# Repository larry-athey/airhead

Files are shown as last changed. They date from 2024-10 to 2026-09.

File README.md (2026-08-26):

# Airhead
Air Still (or clone) upgrade that uses a low-speed PWM driven SSR for heating element control and an ESP32 to make the whole thing smarter. Eliminates that constant full power on/off switching to the heating element and the possibility of scorching. Plus even more features.

You may contact me directly at https://panhandleponics.com<br>
Subscribe to the official YouTube channel at https://www.youtube.com/@PanhandlePonics<br>

_**NEWSFLASH:** If you'd like a far more advanced stand-alone WiFi enabled version of the temperature/power controller that I designed here with the addition of PID for brewing/mashing, check out my [Boilermaker](https://github.com/larry-athey/boilermaker) project!_

**Facebook Idiot:** _Why would you bother?_<br>
**Me:** It's only a "bother" for somebody who couldn't do it on their best day. I'd rather have nicer things.

_...No, I don't use AI to design and build my projects, I actually still know how to use my brain..._

---

Still Spirits brand Air Stills and the various clones all suffer the same design flaw where the temperature is managed the same way it is with an electric cooking appliance. This also includes the ones with adjustable temperature. They send full power to the heating element when heating up, shut it off when they're up to temperature, then repeat this cycle. Thanks for the unstable yo-yo temperatures!

If you have any suspended solids in your wash, they will scorch and fuse to the bottom as they fall out of solution. This will add foul flavors to anything that you're distilling, especially gin. As with my [RPi-Smart-Still](https://github.com/larry-athey/rpi-smart-still) project, this problem is solved by replacing the relays or snap switches on the heating element with a custom low speed PWM _(0.20 Hz)_ and a solid state relay that pulses the power.

As long as the heating element is always running even just a little bit, it will radiate heat upward and force most of the suspended solids to stay afloat. This will eliminate the possibility of scorching for the most part. Just don't try to fill your still with a thick goopy mash.

This project aims to solve that problem and add three user selectable modes:

1. Operate at a constant user selectable power level (1% to 100%)
2. Operate at a constant user selectable temperature (up to 100C/212F)
3. Perform timed runs with a user selectable starting and ending temperature

_Refer to the [Airhead Operation](https://github.com/larry-athey/airhead/blob/main/Instructions/Operation.md) guide for more information on these three modes._

The greatest benefit of the custom low speed PWM and SSR is that it doesn't contribute to premature heating element failure as with the high-speed on/off switching in SCR controllers. SCR phase-angle control generates harmonics _(distortions in the AC sine wave)_ which leads to uneven current distribution, physical vibration, and stress within a heating element. The Airhead is actually better for your boiler's longevity!

The technical definition of the temperature controller in the Airhead is a PI controller, there is no D _(derivative gain)_. The reason for this is because PID controllers will spend more time off than on, once the boiler is up to temperature. This is bad for distillation because there's no thermal velocity to push the ethanol upward out of your wash. The Airhead is intentionally thermally aggressive, unlike a PID controller.

The brains of the operation is a [LilyGo T-Display-S3](https://www.amazon.com/gp/product/B0BLNKPL25/) ESP32 microcontroller with a built-in capacitive touch color LCD display. The boiler control code is a port of the code from my [RPi-Smart-Still](https://github.com/larry-athey/rpi-smart-still) project. This means that even though this is a newer project, the code has already been refined and fine tuned for 2 years in advance.

Refer to the contents of the **/Diagrams/** and **/Instructions/** directories here to learn how to build this project, and be sure to check out the [FAQ](https://github.com/larry-athey/airhead/blob/main/Instructions/FAQ.md).

_**NOTE:** Turn-key kits for those not comfortable with building this from scratch are now available from [my website](https://panhandleponics.com/technology-assisted-distillation/). There may be a short lead time on orders to allow for 3D printing of the 3D models or parts restocking. You may also drop-ship your air still clone to me to have the Airhead upgrade installed and tested with an actual run before I send it to you ready to roll! And it still works out to be less expensive than an original Air Still!_<br><br>

<br><br>
<br><br>
<br><br>
<br><br>
<br>

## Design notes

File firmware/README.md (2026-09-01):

# Firmware Updating

As of the Airhead v1.0.2a source code, end users can now update their firmware over-the-air using a web browser. The initial plan was to provide a USB firmware update utility, but the one that Espressif provides doesn't work like the Arduino IDE does and requires the user to perform circus tricks and learn to use a cryptic program that no non-techie will ever bother with.

To put the Airhead into firmware update mode, turn on the power then press and hold the **Value-** button as soon as the screen lights up. When you see the banner on the screen that says **"Firmare Update Mode"** you can let go of the button.

The Airhead will start up a WiFi access point with the SSID **"Airhead-Firmware-Updater"** and the password to connect is **"12345678"**. Keep in mind that the Airhead is working without an external antenna, so the reliable WiFi range is limited to just a few feet.

Start your web browser and go to **http://192.168.4.1**

<br>

If you are unable to connect, check to make sure that your device pulled an IP address from the Airhead. If it does not pull one, you will need to manually configure a static IP address on your device. Here are settings that will work for you if you encounter this problem.

Address: 192.168.4.100<br>
Subnet Mask: 255.255.255.0<br>
Gateway: 192.168.4.1<br>
DNS: 192.168.4.1<br>

Click on the button to browse to your **airhead-firmware.bin** file and click the blue button to start the upload.

Once the upload progress bar has completed, the Airhead will reboot and will be running the new firmware.

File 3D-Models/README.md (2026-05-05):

All Airhead related 3D models were created by [James "The Doc"](https://www.youtube.com/@TheDocChannel) from Ireland. Keep in mind that the 3D models for the spacer ring halves may require rotation in Cura _(or whatever slicer you use)_ in order to fit on your print bed. The full spacer ring will require a printer with at least a 300x300 mm bed.

The model **Airhead Inside Plate.stl** is only necessary if you are installing an Airhead in a metal Air Still clone that came with a built-in adjustable temperature controller. Removing the stock controller leaves a large rectangular hole where the bolt holes would be drilled in a plastic-body clone. This plate covers that hole from the inside and provides the two bolt holes and a wire pass-thru hole.

3D models in the **uBM** folder are for the μBoilermaker (Micro Boilermaker), see [uBoilermaker.md](https://github.com/larry-athey/airhead/blob/main/Instructions/uBoilermaker.md) for more information.

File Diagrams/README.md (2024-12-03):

The schematic for the PSU and interface is just for the most basic connection using a solid state relay. If you intend to use an SCR board, there may or may not be additional components involved.

If you are using a PWM controlled SCR board, chances are that it already has an opto isolator onboard to protect the original PWM controller that it was designed for. No additional circuity should be needed.

If you are using a voltage controlled SCR board, you will need an optically isolated [PWM to voltage convertor](https://www.amazon.com/dp/B0BG2G5FMX) which will require an additional buck regulator due to its power supply requirements.

_**NOTE:** If you are going to be using an SCR board of any type, you will need uncomment the **SCR_OUT** constant in the ESP32 code in order to enable the 2 KHz PWM output. The default 0.20 Hz PWM used for SSR support is far too slow for use with any SCR board._

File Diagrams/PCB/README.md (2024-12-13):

Printed circuit board for the Airhead PSU and Interface, designed by [James "The Doc"](https://www.youtube.com/@TheDocChannel) from Ireland. This PCB supports PWM or voltage controlled SCR boards, and can be used with a solid state relay by simply soldering wires to the board to connect to the control side of your SSR. These wires would be connected to any ground hole and the center pin for the PWM/+5V jumper.

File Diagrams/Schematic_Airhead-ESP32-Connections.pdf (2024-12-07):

A | A

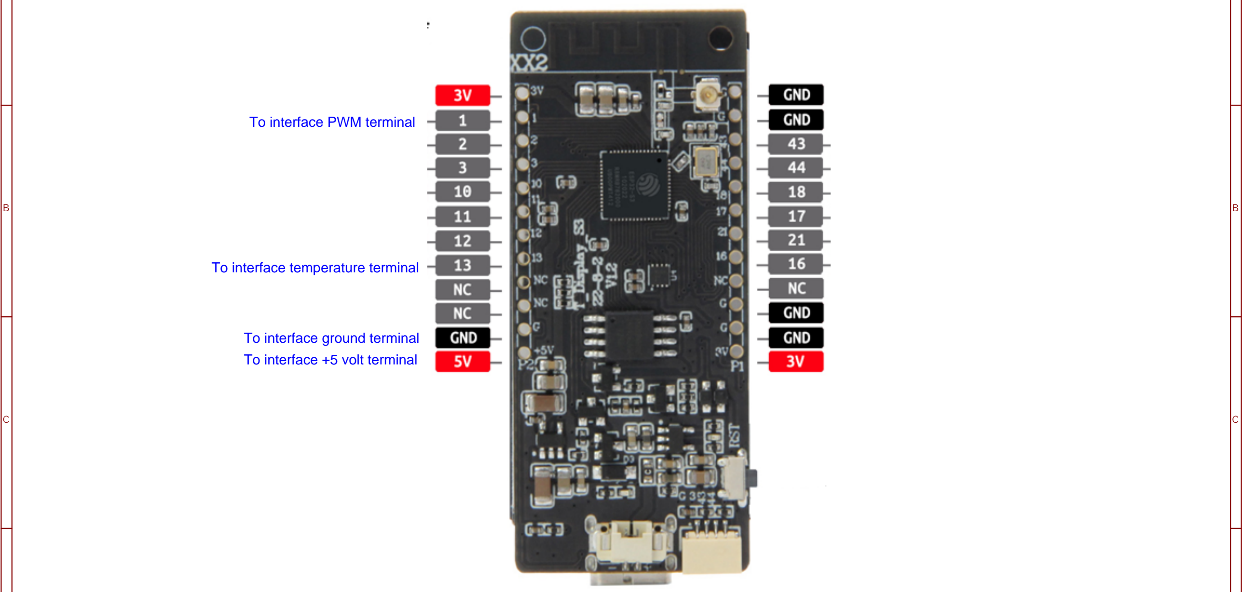
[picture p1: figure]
To interface +5 volt terminal; To interface ground terminal; To interface temperature terminal; To interface PWM terminal

D | D

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
TITLE:
Airhead ESP32 Connections | REV: 1.0
Date: | 2024-12-02

Sheet: 1/1
Drawn By: Larry Athey

Company: Panhandle Ponics R&D

LilyGo T-Display-S3 Bottom View

USB-C Port

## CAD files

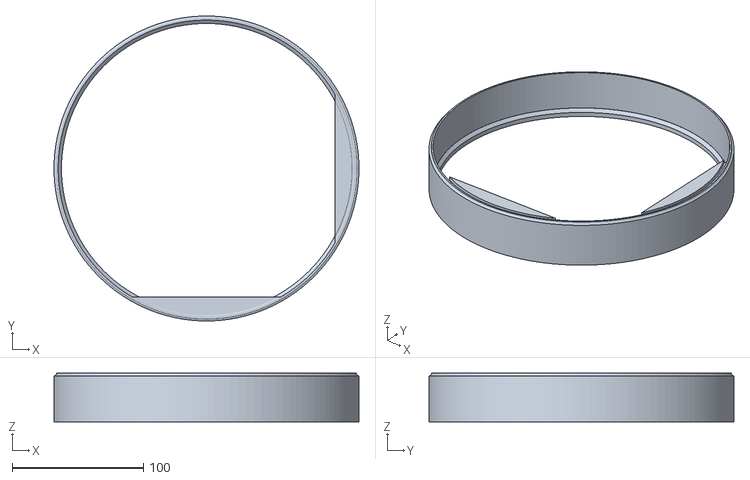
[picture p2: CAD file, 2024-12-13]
3D-Models/Air Still Spacer Ring/Spacer Ring Full.stl
232.3 x 232.3 x 37.0

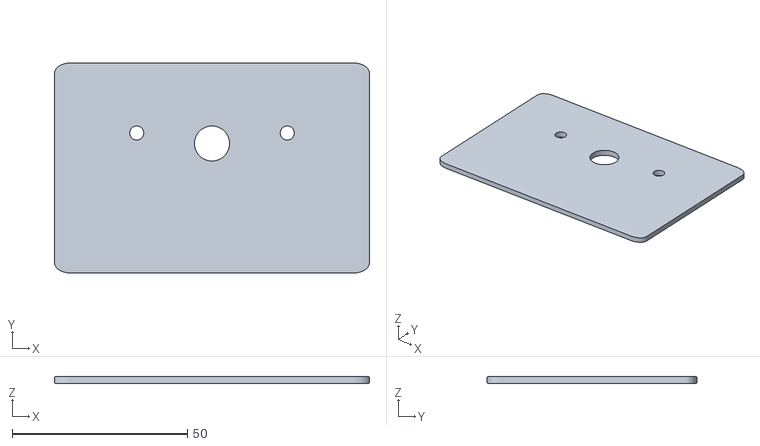
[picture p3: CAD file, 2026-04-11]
3D-Models/Airhead Inside Plate.stl
90.0 x 60.0 x 2.00

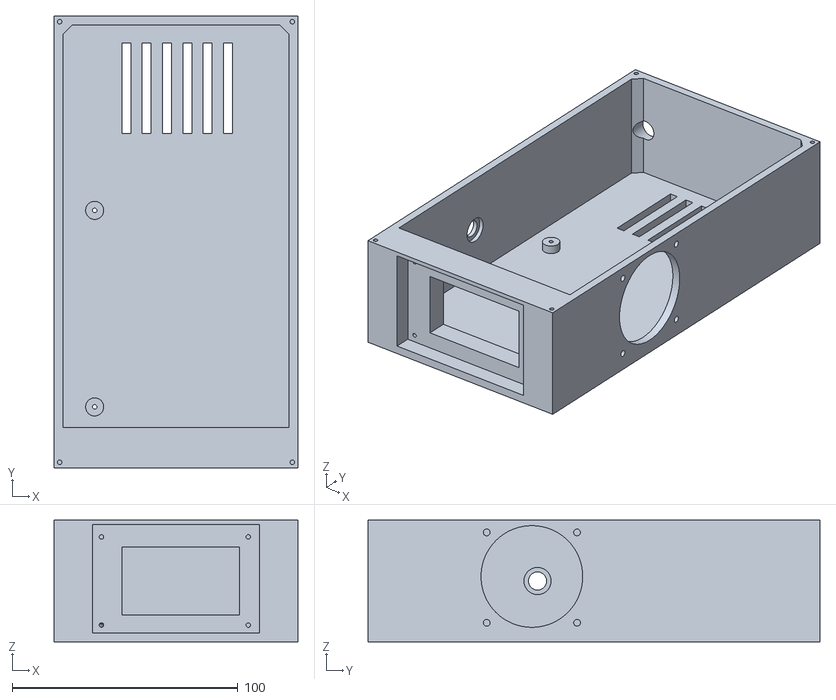
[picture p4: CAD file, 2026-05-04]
3D-Models/uBM/uBM-Case-Bottom.stl
108.0 x 200.0 x 54.0

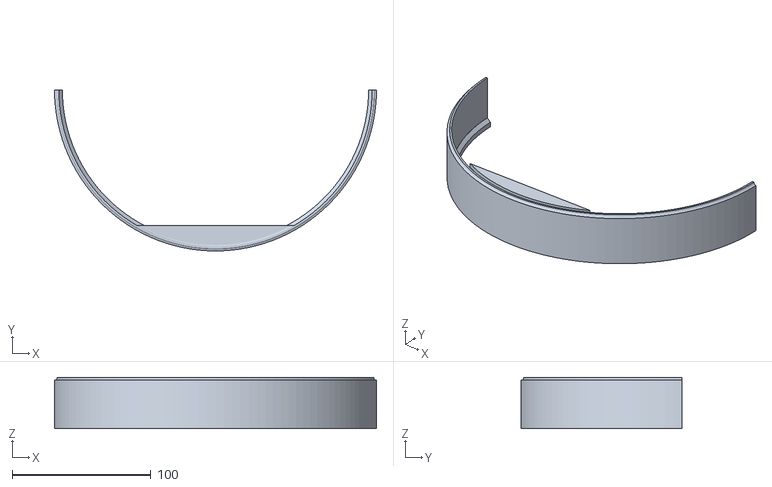
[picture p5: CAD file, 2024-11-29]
3D-Models/Air Still Spacer Ring/Spacer Ring Half.stl
232.3 x 116.1 x 37.0

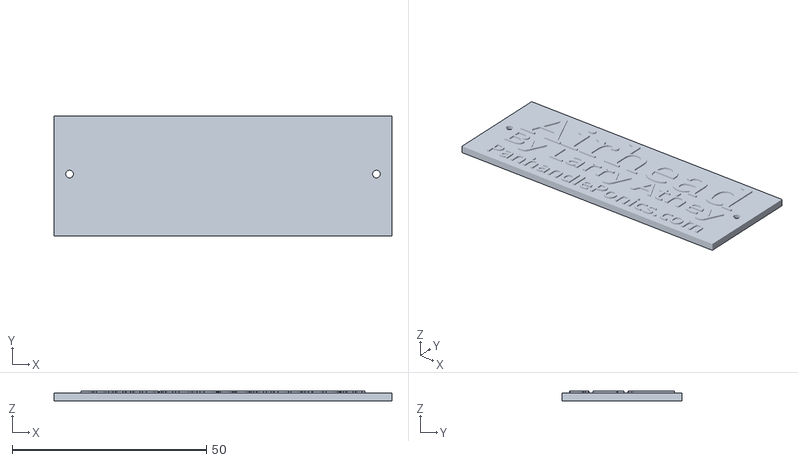
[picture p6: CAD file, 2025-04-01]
3D-Models/Airhead-Badge.stl
87.0 x 31.0 x 2.50

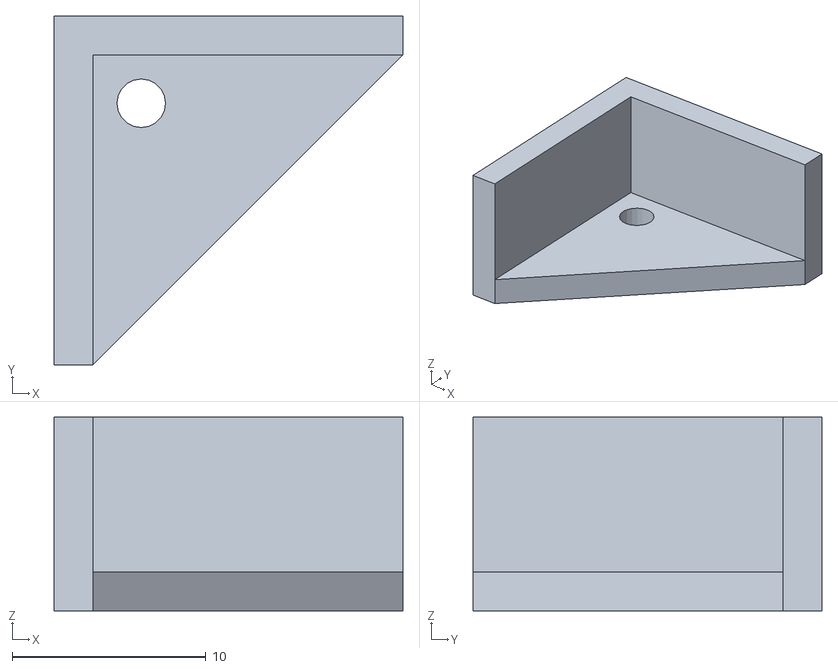
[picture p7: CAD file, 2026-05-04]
3D-Models/uBM/uBM-Corner-Cap.stl
18.0 x 18.0 x 10.0

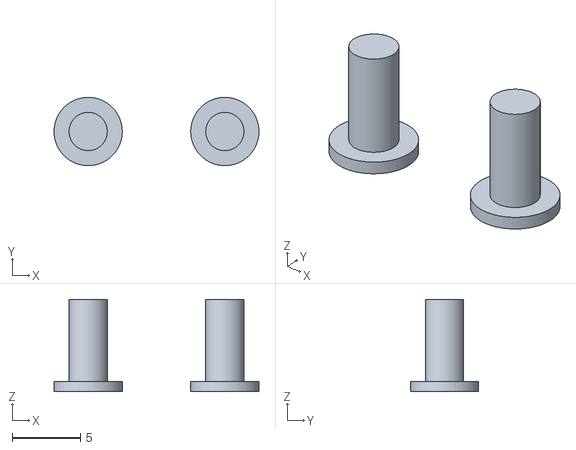
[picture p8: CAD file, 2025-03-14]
3D-Models/Airhead-Buttons.stl
15.0 x 5.00 x 6.75

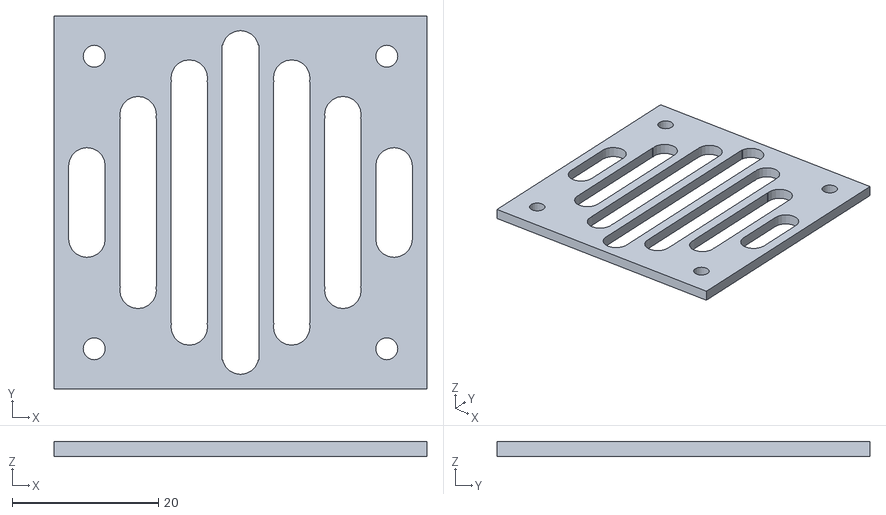
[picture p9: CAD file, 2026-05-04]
3D-Models/uBM/uBM-Fan-Cover.stl
51.0 x 51.0 x 2.00

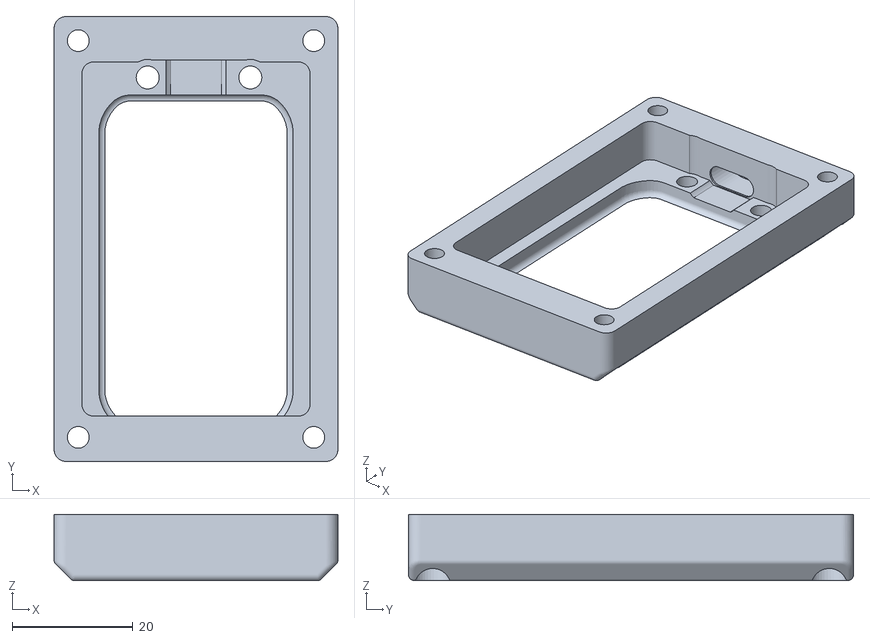
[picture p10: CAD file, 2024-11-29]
3D-Models/Airhead Case Front.stl
47.0 x 73.7 x 11.0

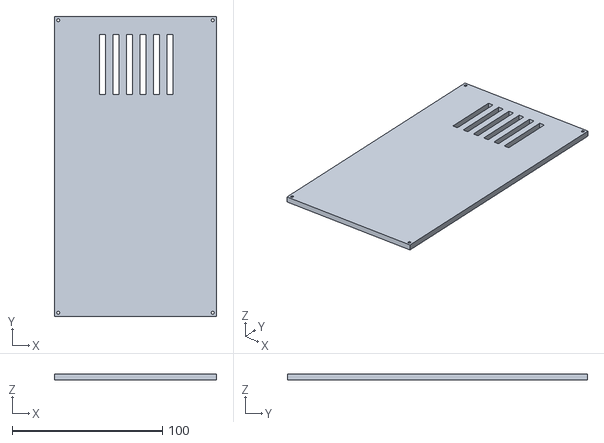
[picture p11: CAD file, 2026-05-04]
3D-Models/uBM/uBM-Case-Top.stl
108.0 x 200.0 x 4.00

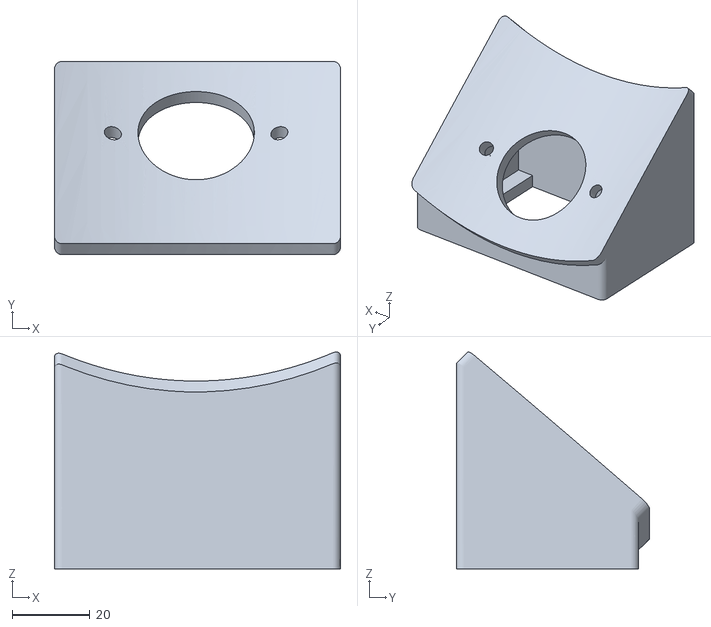
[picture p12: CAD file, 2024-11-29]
3D-Models/Airhead Case Back.stl
73.7 x 49.8 x 55.9

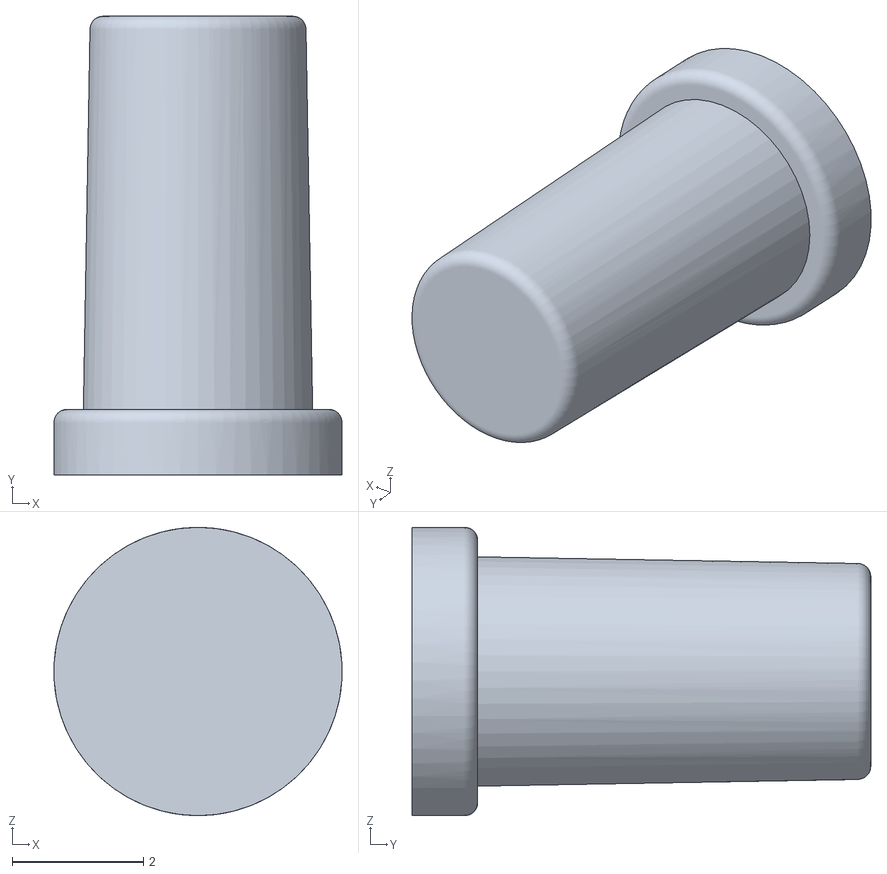
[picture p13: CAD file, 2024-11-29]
3D-Models/Airhead Button.stl
4.40 x 7.00 x 4.40

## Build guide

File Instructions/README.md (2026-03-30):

# Airhead Turn-Key Kit

For those who aren't up to [component level](https://github.com/larry-athey/airhead/tree/main/Instructions/DIY-Build) electronics work and 3D printing, [Airhead turn-key kits](https://panhandleponics.com/technology-assisted-distillation/) are available from my website for $140 plus shipping in the USA where the USPS flat-rate box coverage area applies. Installation requires no soldering and only basic tools. Orders to Alaska and Hawaii require a special URL to be emailed to you due to the added shipping expense.

Please keep in mind that I'm not running a full blown mail-order operation. I only have four 3D printers and only one that is large enough to print the Airhead spacer ring. Each of these kits take 12 hours to print all parts, so I'm only capable of building and testing one Airhead every 3 days. My other three printers are pretty much dedicated to printing [Boilermaker](https://github.com/larry-athey/boilermaker) cases which I can also only build and test one every 3 days.

# Installation Guide Video

I have put together the video [Airhead Installation Using a Vevor Air Still](https://youtu.be/vFivj2nX99s) to show people how to install the Airhead Turn-Key Kit in a Vevor water distiller. I also offer people the option to drop-ship their Vevor air still clones to me to have the Airhead installed and tested with an actual run before shipping it out to them. It's only slightly more than the price of the kit alone and saves you the trouble of installing it yourself. Again, orders to Alaska and Hawaii require additional shipping fees.

I also put together the video [Airhead + Air Still Full Demo](https://www.youtube.com/watch?v=bEKPDaXU4ro) that shows how to use the Airhead after it's installed. This example shows how to distill wine in order to get high-proof brandy out of it. You can also use the Airhead to make gin and to even clean up whiskey that you may have over-oaked. Just make sure that the overall body of liquid in the still is no more than 40% ABV or things could go BOOM!

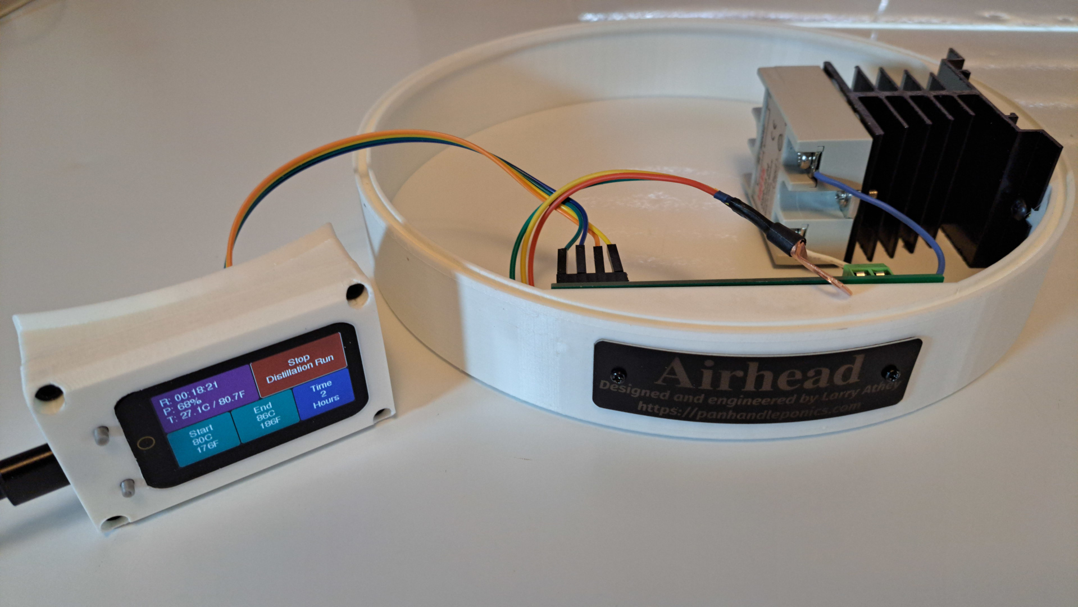
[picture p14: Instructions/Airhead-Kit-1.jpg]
<br>

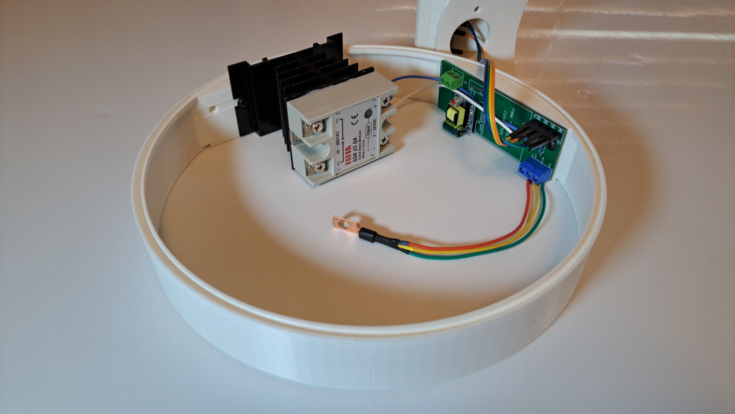
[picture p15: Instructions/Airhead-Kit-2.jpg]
<br>

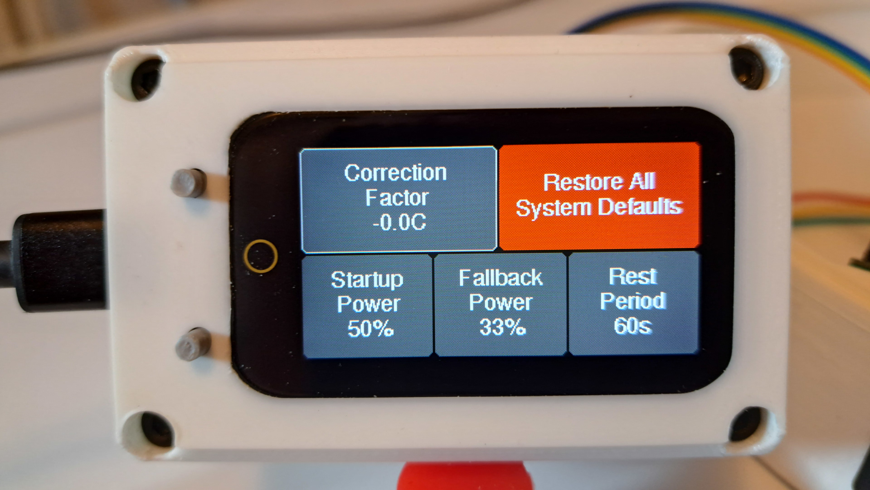
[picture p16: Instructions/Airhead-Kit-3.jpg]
<br>

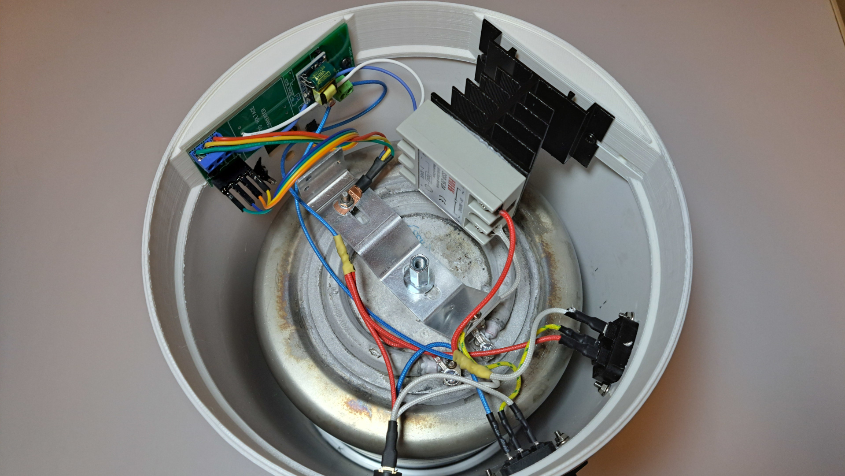
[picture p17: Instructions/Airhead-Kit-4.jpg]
<br>

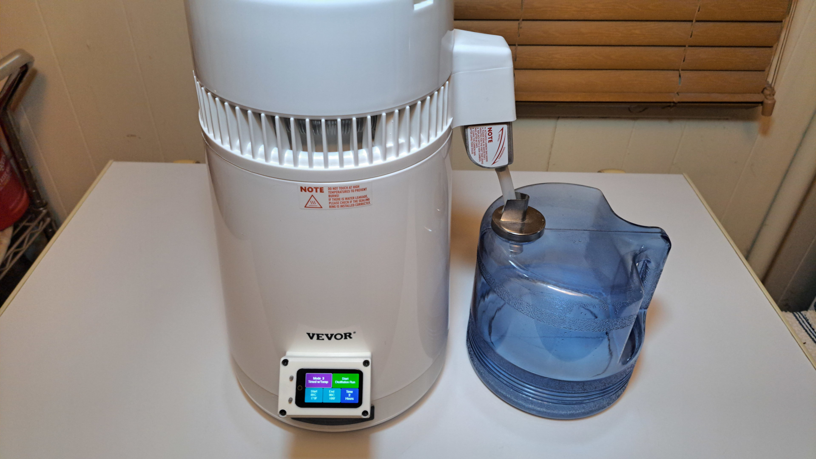
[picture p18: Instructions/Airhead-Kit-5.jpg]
<br>

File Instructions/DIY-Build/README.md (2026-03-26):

# DIY Build Assembly Instructions

_The following instructions are for **modifying** an Air Still (or clone). Personally, I would recommend just gutting the unit and rewiring the unit from scratch according to the [Airhead Implementation](https://github.com/larry-athey/airhead/blob/main/Diagrams/Schematic_Airhead-Implementation.pdf) schematic without the temperature snap switch or the circuit breaker that kicks if it boils dry. The Airhead Code already has protection built-in that shuts down the run if the boiler temperature exceeds 103C/217F. It's clear that these devices are not built to any solid standards, so it's really not possible to create a one-size-fits-all set of modification instructions._

In these examples, I'm using a cheap $65 [Vevor water distiller](https://www.amazon.com/dp/B0CN2SBJLT). No need for an expensive original Air Still for this project. For the sake of simplicity, I will be setting up this Air Still clone to use a solid state relay as a simlified PID controller rather than an SCR board. You can also use a solid state relay like an SCR board at a much lower frequency, refer to the source code comments. Anyway, the first step is to turn your Air Still upside down and remove the bottom cover.

Referring to the photo **Air-Still-Default-Wiring.jpg** here. The white wires are connected to the thermal control snap switch and are the AC neutral connection to the heating element. The blue wires are for an LED power indicator on the front of the still. The red wires are from the AC hot side and go to a circuit breaker on the front of the still and then come back to connect to the other side of the heating element. Lastly, the yellow wires are the earth ground of the AC connection and connect to the body of the boiler vessel.

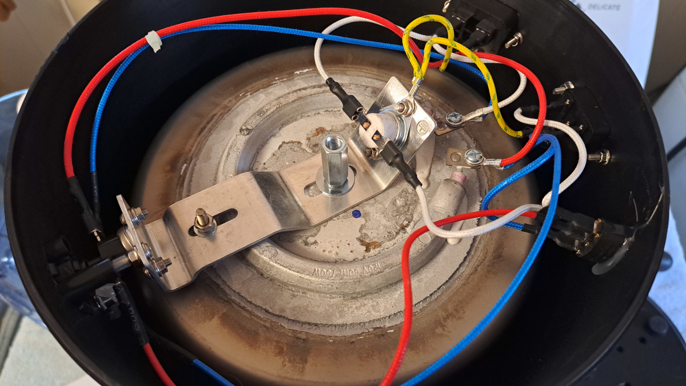
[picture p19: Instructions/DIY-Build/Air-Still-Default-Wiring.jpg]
<br>

You will now need to remove that aluminum bracket so you can remove the power indicator, the button for the reset breaker, and the snap switch that currently controls the temperature. We will not be removing the reset breaker, but it will likely never be used since the Airhead brain will shut down the unit if it ever goes over 103C/217F. You can clip the wires to the power indicator and strip them back since they will be used to power the Airhead controller system. The wires to the snap switch will be connected to the solid state relay.

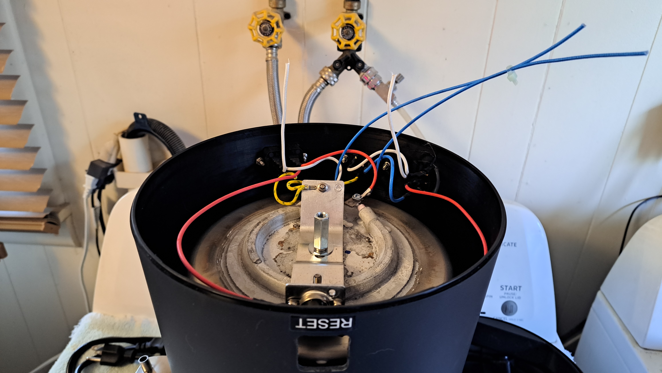
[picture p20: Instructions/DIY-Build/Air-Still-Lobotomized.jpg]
<br>

As you can see in the photo **Air-Still-Lobotomized.jpg** above, everything that I mentioned has been removed and the aluminum bracket has been put back in place. I slid it back as far as it would go since the reset breaker will likely never need to be used unless something goes seriously wrong. We have the blue wires that will be connected to the Airhead power supply and interface board, and the white wires which will be connected to the load side of the solid state relay. You may or may not need to extend the white wires.

_**NOTE:** Depending on your Air Still (or clone) model, the manufacturer may have put the fan on the switched side of the heating element. This is an absolutely stupid plan, the fan should run continuously. The temperature control should only run the heating element. This will require a simple wiring modification if yours has this problem. Lucky me, this unit actually has that exact design flaw._

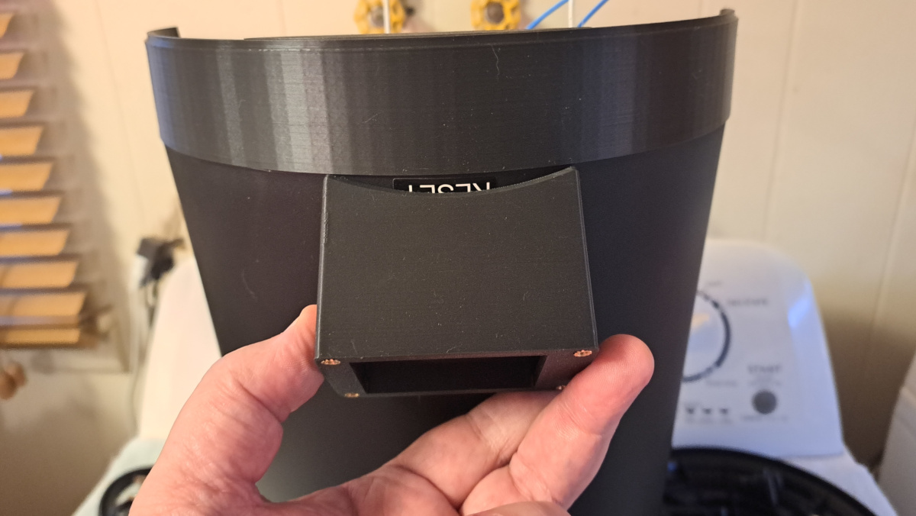
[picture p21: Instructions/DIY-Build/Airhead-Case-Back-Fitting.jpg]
<br>

As demonstrated in the photo **Airhead-Case-Back-Fitting.jpg** above, you need to align the back part of your Airhead case over the hole that the reset button was removed from. It's best if you set your spacer ring in place to get your vertical alignment correct. You should mark the two screw holes using a pencil, or small paint brush and paint, or nail polish if you happen to have that at home. Carefully drill the holes while avoiding damage to the boiler vessel inside. Then attach the case with nuts and bolts, paint the threads to lock the nuts in place.

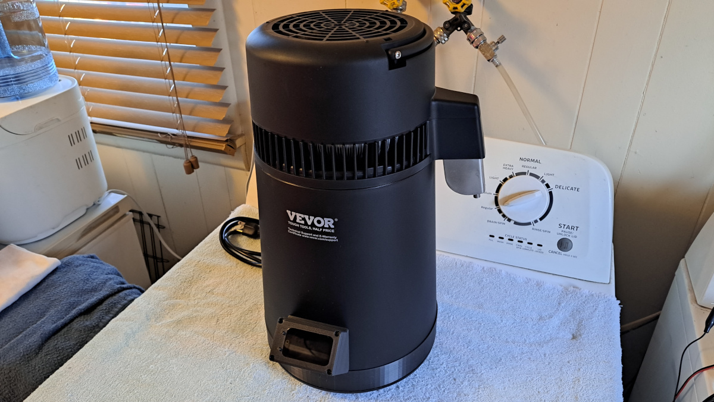
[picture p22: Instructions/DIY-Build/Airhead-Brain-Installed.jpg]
<br>

As you can see in the photo **Airhead-Brain-Installed.jpg** above, the Airhead brain is installed in its case and it doesn't interfere with the seating of the spacer ring. This is just a dry fitting test before we procede with the wiring. Please keep in mind that the wiring steps that follow are using a prototype power supply and interface board. The Airhead kits that I will be selling on my website will come with an actual custom designed printed circuit board. I just don't have them at this time since they have to be ordered from China in bulk.

_**NOTE:** If you are using the same Air Still clone that I'm using, you will need a [6mm-1.00x70mm bolt](https://www.amazon.com/VGBUY-Stainless-Spanner-Included-VG30115/dp/B0CK1RQWGH/) to reattach the bottom after the spacer ring is in place. Other brands may use a different method to attach the bottom, I have another brand that uses 3 screws._

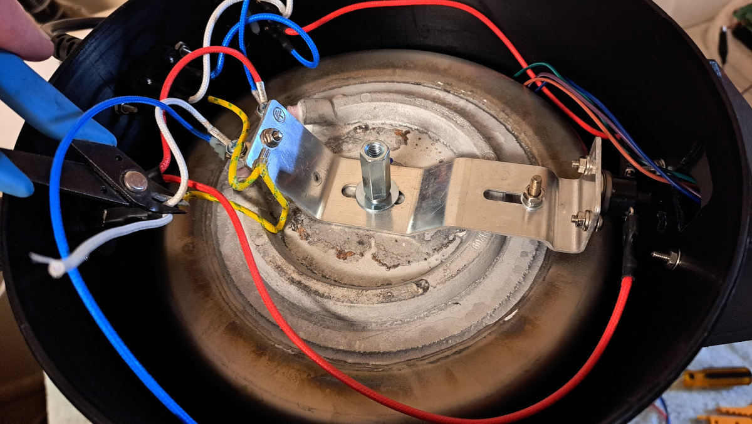
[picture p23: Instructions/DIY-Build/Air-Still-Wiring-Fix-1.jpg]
<br>

As you can see in the photo **Air-Still-Wiring-Fix-1.jpg** above, the bottom connection of the heating element has one of the blue wires and a white wire connected to it. If we were to leave things as is and connect the two white wires from the snap switch to the solid state relay, the entire system would never turn on. If it did, the entire system including the fan would turn off as soon as it's up to temperature. This is the stupid plan that I was referring to. Cut that white wire connected from the element to the fan power socket.

_**NOTE:** Don't panic, the goal here is just to have all of the neutral lines connected together, except for the neutral side of the heatng element._

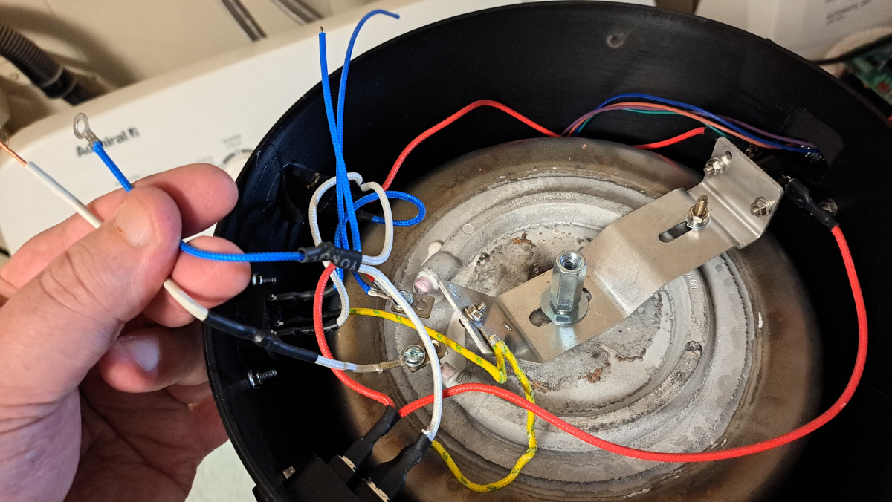
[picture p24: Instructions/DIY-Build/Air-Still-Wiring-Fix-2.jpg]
<br>

Looking at the photo **Air-Still-Wiring-Fix-2.jpg** above, you can see that the white wire that was clipped has been extended about 4 inches. This connects to one of the screws on the load side of the solid state relay. The blue wire was removed the the bottom side of the heating element, cut in half, and then joined together with the two white wires that were connected to the snap switch that was removed. The blue wire with the eyelet connector on the end connects to the other screw on the load side of the solid state relay.

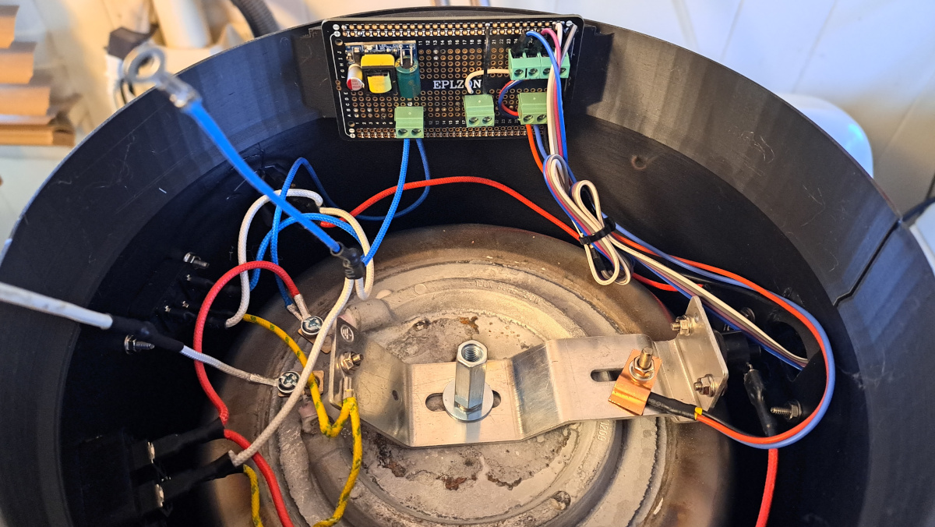
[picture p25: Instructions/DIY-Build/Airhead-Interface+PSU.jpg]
<br>

As you can see in the photo **Airhead-Interface+PSU.jpg** above, the prototype interface and PSU board has been attached to one of the spacer ring halves. The two blue wires with the stripped ends have been connected to the AC input terminals. The Airhead brain ribbon cable and the DS18B20 temperature sensor have also been connected. The temperature sensor has been installed under a copper heat sink clip against the aluminum bracket. Thermal transfer compound shouldn't be used in this case.

Airhead brain connector, left to right:
1. Temperature, ESP32 GPIO 13
2. PWM, ESP32 GPIO 1
3. +5 volts
4. Ground

Temperature sensor connector, left to right:
1. +5 volts
2. Data
3. Ground

PWM/SSR connector, left to right:
1. +3.3 volt PWM output
2. Ground

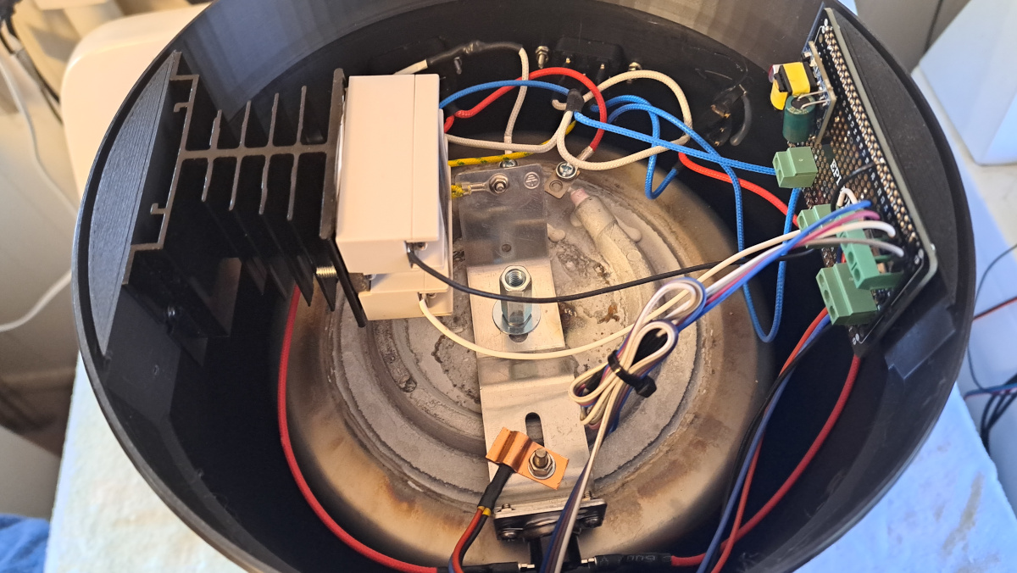
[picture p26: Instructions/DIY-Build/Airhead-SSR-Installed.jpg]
<br>

Finally, as shown in the photo **Airhead-SSR-Installed.jpg** above, the solid state relay is installed and wired in. The heat sink isn't really necessary, this SSR just came with one so I went ahead and used it to show that there actually is room for one. The documentation for these states that a heat sink isn't needed until a 1200 watt load is on it. The heating element used in these appliances is only 700 watts.

_**NOTE:** If you think your temperature sensor is picking up too much heat from the heating element in the location shown in the photos, move it over where the snap switch was installed. That region of the aluminum bracket is further away from the heating element and has more free air around the mounting point. This will tame down its readings a little bit and may be beneficial to your use of the still. If you applied thermal transfer compound, you may also want to try wiping it off test things again._

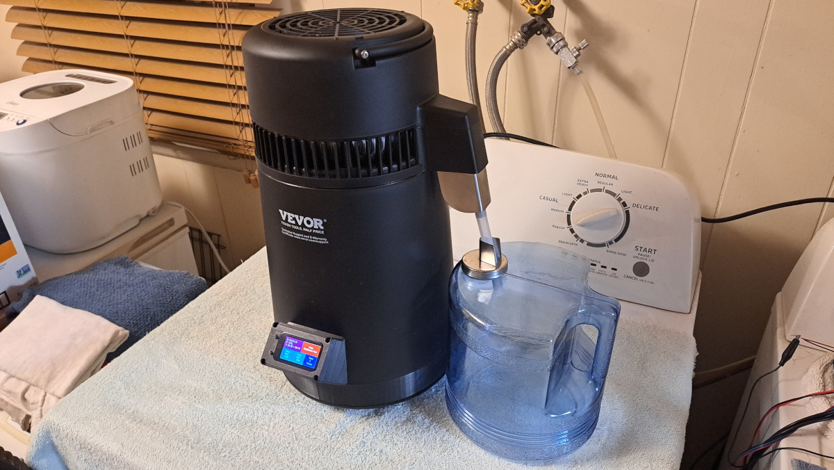
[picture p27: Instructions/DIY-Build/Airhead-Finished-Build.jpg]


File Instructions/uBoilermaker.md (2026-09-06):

# μBoilermaker (micro Boilermaker) 



---

The μBoilermaker is 100% based on the Airhead, but is a stand-alone boiler controller for 120 volt resistive loads up to 1500 watts and uses an autotuning PID controller, unlike the aggressive PI controller used by the Airhead. You can switch any Airhead to μBoilermaker mode by holding the Value+ button for 15 seconds after you have selected Mode 3. Use the same procedure to switch things back.

The reason for the μBoilermaker is to satisfy the numerous requests for a Boilermaker that isn't WiFi dependent. This isn't a one-to-one implementation of the full Boilermaker, but it provides a person the ability to have constant power, constant temperature, or timed runs with progressive temperature. It also uses a preset **Cruise Then Brew** mode and runs in PI control until 1C below the target temp.

Unlike the full Boilermaker, these are sold on my website as 120-volt-only and bench/counter top only. The size of the case only allows for 14 gauge grounded power cables and they only ship with an SSR-40DA solid state relay mounted to the same heat sink used in the Airhead. These are priced the same as the full Boilermaker with 120 volt pigtails, they're just a smaller version with a touch screen.

[Operation](https://github.com/larry-athey/airhead/blob/main/Instructions/Operation.md) of the μBoilermaker is completely identical to the Airhead, the only real difference are the options on the calibration page which are PID gain parameters. The target audience for these are people using stove-top stills with an electric hot plate, home beer brewers, and people who want far better control over an electric smoker, all without the need for a WiFi connection.

### How to run PID autotune:

1. Fill the boiler to its normal full mark with water.
2. Select Mode 3.
3. Hold **Value+** for at least 5 seconds, then press **Value-** at the same time.
4. The test takes 5–15 minutes. Watch the screen for progress.

After tuning completes, the new **P, I, and D** values will be saved. You can manually tweak them on the calibration page if needed.

### What is PID? (simple version)

PID is a control method that tries to reach and hold your exact target temperature smoothly:

- **P (Proportional)** — How strongly it reacts to being off-target.
- **I (Integral)** — Corrects small long-term errors (like slowly drifting a bit low).
- **D (Derivative)** — Looks at how fast the temperature is changing and helps prevent overshooting.

### And now the scientific version

<br>

In the Temperature Cruise mode of the full Boilermaker, the **Change Wait** and **Adjustment Rate** are equal to the **P** parameter and the **Deviation Rate** is equal to the **I** parameter. These values also exist in the Airhead's PI controller, but are static settings.

### Realistic expectations:

- PID gives very steady temperature — great for mashing, fermenting, sous-vide style control, or electric smokers.
- It is **not** as thermally aggressive as the normal Airhead PI mode. Once at temperature it will pulse the heater more gently, so you will see significantly slower vapor production in distillation.
- The temperature control becomes more stable the longer it runs because the PID is training itself on the current load.
- Autotune results are a good starting point, but every boiler/setup is different. Feel free to tweak the numbers ±20–50% and test.

_**NOTE:** If you are using an electric hot plate, you will want to bypass its internal temperature control dial or it will interrupt your power once you reach its maximum temperature. It's also recommended that you maintain good ventilation under it because most also have a thermal snap switch that will cut out if it overheats internally. The μBoilermaker does not work with inductive cooktops!_

---



---



---



---



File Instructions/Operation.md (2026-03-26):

# Airhead Operation

<br>

As you have probably noticed by the photos on the front page of this GitHub repo, the Airhead has three operating modes. Each of the modes are user configurable and your last used settings will be restored each time you start up your still. In temperature managed modes 2 and 3, the temperature is checked every 30 seconds and the power is adjusted accordingly. The temperature is managed to +/- 0.2C/0.36F in order to maintain a fair level of accuracy at temperatures down to 38C/100F without beating the CPU to death. 

**Mode 1** maintains a constant power level with no temperature management whatsoever. You may adjust the power level from 1% to 100%. This mode would be used for simmering liquids, calibrating the Correction Factor setting, or distilling water if you set the power level to 100%. There is a safety feature that will shut down your still if you boil out all of the water. This safety feature kicks in at 103C/217F.

**Mode 2** maintains a constant temperature and automatically adjusts the power. If you fill your still with room temperature wash/wine and you set the temperature to 80C/176F, it may take 30 minutes at sea level to reach the minimum operating temperature. The power level starts out at 50% and progressively increases by 1% every minute until the target temperature is reached. At that point, the power will fall back to one third (33%) and rest for 1 minute before temperature management begins. Distillate usually starts in 10 minutes.

**Mode 3** is a timed distillation run where you set a starting and ending temperature. The time is selected in hours and the target temperature is adjusted _(up or down)_ every 15 minutes. This is primarily for distilling spirits. For example, you would do a 2 hour run starting at 80C/176F and ending at 86C/186F. This is a common method used by those who bought Air Still clones with manual temperature control to squeeze out as much product as possible. This mode frees you from performing manual temperature changes.

If you are at a higher altitude, such as the "Mile High City" (Denver, CO) you will notice that water boils way faster. After your Airhead performs the 33% fallback when the minimum operating temperature is reached, you will likely see the power level adjust down instead of up. It should come as no surprise to see it adjust down to 18% to 20% to maintain water at 80C/176F, this is absolutely normal.

Keep in mind that a higher ABV wash (15% or greater) requires less heat at the beginning than a lower ABV wash. This needs to be kept in mind when you are setting your temperatures in Mode 3. If you aren't getting distillate until the end of a Mode 3 run, your ABV is too low. Increase your wash ABV or increase your temperature range.

_**NOTE:** As of the version 1.0.2 source code release, the startup and fallback power levels specified in the two temperature managed modes are now configurable. If you press the home button to the left of the screen (the gold circle) it will switch the Airhead into configuration mode. From this screen, you can configure the correction factor for the temperature sensor from -15C to +15C. You can also configure the startup and fallback power levels from 1% to 100% as well as the rest period after the boiler is up to temperature from 1 second to 255 seconds. Lastly, there is a button that also allows you to do a full reset of all settings back to their defaults._

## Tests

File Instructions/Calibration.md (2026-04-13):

# Calibration

<br>

Calibrating the correction factor of the Airhead temperature sensor is actually stupid-simple and only requires you to know your altitude above sea level. Water boils at 100C/212F at sea level and that temperature drops by 0.5C/1F for every 500 feet you are above sea level. So in my case where I'm 4000 feet above sea level, water boils at 95.5C/204F.

Keep in mind that an immersion thermometer isn't the most accurate way of comparing the readings to determine the correction factor. If you were to use one, an old analog unit that works using a bi-metal coil would be the most reliable one since they aren't affected by the EMF noise that comes from the heating element. A water boil calibration will always be the most reliable method.

## How to perform a water boil calibration

1. Reset the Correction Factor to 0.0C
2. Fill the still with plain water
3. Switch to mode 2 and set the target temperature to 100C/212F
4. Put the lid back on, plug it in, and start the run
5. Make a note of the temperature when you start seeing the first steady water drops coming out
6. Stop the run, go back to the configuration page and adjust the Correction Factor as needed
7. Retart the run, you may want to add a couple ice cubes to cool down the water first
8. Note the temperature when steady water drops start coming out again _(see the note below)_
9. Repeat until you have the sensor dialed in, it doesn't have to be dead accurate

Keep in mind that barrometric pressure can affect this, but not by a whole lot. You could easily see your boiling temperature go up or down by 0.5C/1F depending on the weather. Also keep in mind that some vapor will remain in the condenser every time you stop and restart the boiler, so you can easily ignore the first few drops after a restart.

It's also important to note that even after your air still reaches boiling temperature, you will see the temperature continue to rise. This is just a side effect of the lid being on and causing a pressure increase in the still. The only thing that you should concern yourself with is the temperature when you first start seeing steady drops of coming out on a cold(ish) start up.

After you get your correction factor dialed in, you may wish to write that on the back of the still or label it somehow. This is because any time you tap on the big red button to restore all system defaults, the correction factor will be returned to zero. This will save you from having to do the calibration all over again if you forget that setting.

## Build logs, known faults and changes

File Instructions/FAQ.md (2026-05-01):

# Frequently Asked Questions

Q: I thought it was illegal to own a still in the USA.

A: Nope, not at all. Where do you think distilled water and "essential oils" come from? Because our government is a bunch of money thieving control freaks, they say that you can't distill spirits at home, even though you can make wine or beer at home as strong as you want. You can even freeze homemade hard cider and skim the concentrated ethanol off the top. But they have a problem with home distillers making their beer or wine stronger the easy way. Solution? Simply don't invite them over to watch you and don't distribute it.

---

Q: Can you distill on the grain with this system?

A: No, there's a huge difference between suspended solids and a bucket of mash. To distill on the grain, you need a boiler with a motorized paddle or agitator. Suspended solids would refer to small particles or botanicals that you would use for making Gin.

---

Q: Why does a thermometer in the boiler show a higher temperature than I see on the screen?

A: An immersion thermometer is reading the liquid temperature and the Airhead thermometer is reading the vessel temperature. This is why they used a 150F snap switch to open up when the water in the boiler hits 212F. Press the home button _(the gold circle to the left of the screen)_ to enter configuration mode. You can adjust the temperature sensor correction factor -15C to +15C to dial in your sensor readings. Be sure that your temperature sensor is installed with thermal compound for the best results. For more details, see the page [Configuration.md](https://github.com/larry-athey/airhead/blob/main/Instructions/Calibration.md)

_**NOTE:** The +/- 15C (or +/- 27F) correction factor range is effective for a theoretical altitude up to 13,500 feet above sea level. If you are needing to apply an unreasonably high correction factor, then you have a thermal conductivity problem with the temperature sensor. Make sure that you are using thermal compound when installing the temperature sensor or mount it under the double-nut on the center bolt that holds the bottom cover on. You will likely need to use a negative correction factor after this._

---

Q: Why does it seem like you have something against PID controllers?

A: I don't, but they just have no place in distillation, especially in a pot still. Precision targeted temperature control is really only useful in brewing and an Air Still is entirely too small for that. I realize that George Duncan championed PID controllers, but they only work in distillation if you're running a hard boil because they'll go lazy at ethanol boiling temperature and then you'll lose all thermal velocity. Nobody bought an Air Still for a 1 gallon 80C/176F pot still distillation run to take 4 to 8 hours to complete.

_**NOTE:** A test using an 80C/176F to 86C/186F progressive run redistilling a gallon of 80 proof vodka takes 2 hours with the Airhead's default PI controller. Switching to the hidden μBoilermaker (micro Boilermaker) mode which uses PID, the run takes 4 hours to accomplish the same amount of 140 proof output._

---

Q: Is there some kind of "rule of thumb" that you follow for the Mode 3 temperatures?

A: Sort of, but it's just based on basic physics. The higher your starting ABV, the lower your starting temperature needs to be since ethanol has a lower boiling point. If you're starting with a low ABV, then you need a higher temperature to force the ethanol out **before** you start getting water vapor. In cases of distilling anything 12% ABV or less, you can actually just set the starting and ending temperatures to 86C/186F and let it run for 2 hours. If you're making gin, then you'd start around 80C/176F and end at 86C/186F.

---

Q: Why does it appear that you do everything in celcius and fahrenheit is an after-thought?

A: Because that's just the way the world works. The temperature sensor used in the Airhead outputs its readings in celcius and bloating the code with bidirectional temperature translations just to satisfy one country on the planet doesn't make sense. Unlike a normal computer, an ESP32 doesn't have an endless pool of storage space and RAM. But, that's the beauty of open source, create your own fork of the code and bloat it if you want to. 45+ years of programming has taught me that wasteful coding equals crappy performance.

---

Q: Why am I getting such low-proof distillate?

A: You're likely running your temperature entirely too hot. Start with a target temperature of 80C/176F and feel the air blowing out the top of the still when ethanol starts flowing. You'll notice that the air is mostly cool. Then try a target temperature of 88C/190F and feel the air, it will feel much warmer. This is because you're getting water vapor into the condenser which carries much more heat and you will water down your distillate. Avoid going over 86C/186F unless you intentionally want to water it down.

---

Q: I dumped a 6-pack of PBR in my still and didn't get more than a few drops out of it. Why?

A: Well, that's about the best thing you can do with that beer. Your problem is two-fold, you first need to use totally flat beer and you should always fill up the boiler to its full line. The first part of your problem is that the ethanol vapor is trapped under the beer foam. The second part is that the small volume of liquid causes your temperature sensor to reach operating temp faster because there isn't enough liquid to rob heat from the boiler vessel _(thermodynamics is an interesting physics study)_.

---

Q: How do you deal with methanol with these? I'm not in a hurry to go blind.

A: The first step is to quit paying attention to old wive's tales and prohibition era propaganda. You couldn't possibly create enough methanol with one of these little stills to blind you, or even one 10 times its size. Buy a gallon of apple juice and drink it moderately fast, like within an hour. Then an hour after that, ask yourself why you have a headache. It's because there is naturally occuring methanol in apple juice, you just gave yourself a hangover without drinking any booze at all. Be careful what you worry about in life.

---

Q: What is the benefit to using a progressive temperature in mode 3?

A: If you were to run at a set target temperature of 80C/176F, it could take you 6 hours or more to get all of the ethanol out. Your output slows down as the ethanol is removed and you may only see one drop per minute after a couple hours, even though there's still a decent amount of ethanol remaining inside. Starting at 80C/176F and ending at 86C/186F over 2 hours will achieve the same result in far less time. 

---

Q: What are the popping noises that I keep hearing coming out of the still?

A: That's vapor condensing back into a liquid and blocking the air path, it's just bubbles popping. Nothing to be alarmed about, there is nothing broken. It's just because the condenser used here is mostly horizontal rather than vertical like larger stills.

---

Q: What is the highest proof that you can get out of one of these stills?

A: The highest I've ever gotten was 140 and that was from a Gin redistillation run at a constant 80C/176F over 6 hours, but I've heard of others redistilling a gallon of 80 proof vodka and get 162 proof out of it on a progressive run. Distilling normal stuff like wine to make Brandy, usually ends up being between 120 and 130 on a 2 hour progressive run.

---

Q: Can you use one of these to tame down something that was aged on too much char?

A: Absolutely! Just be sure to do a vinegar run afterwards because it will leave char on the inside of the condenser. Knock your existing hooch down to 80 proof first and then redistill it at 80C/176F to 86C/186F so water vapor doesn't carry the char flavor through. Knock the secondary distillation down to anywhere from 110 to 120 proof and age it again with less char. Any higher proof and you will end up drawing undesirable flavors out of the wood.

---

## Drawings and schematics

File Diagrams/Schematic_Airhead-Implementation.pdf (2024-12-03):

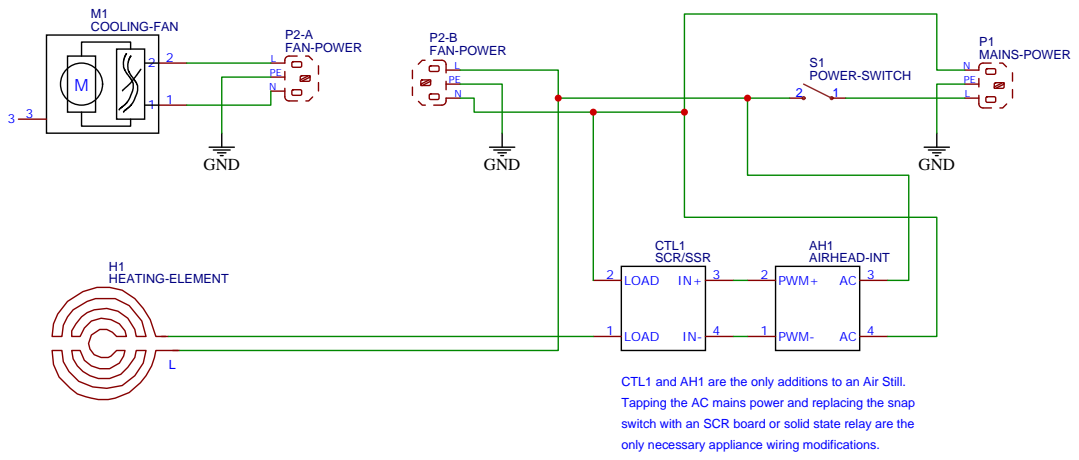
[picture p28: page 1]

CTL1 and AH1 are the only additions to an Air Still.
Tapping the AC mains power and replacing the snap
switch with an SCR board or solid state relay are the
only necessary appliance wiring modifications.

Drawn By: Larry Athey

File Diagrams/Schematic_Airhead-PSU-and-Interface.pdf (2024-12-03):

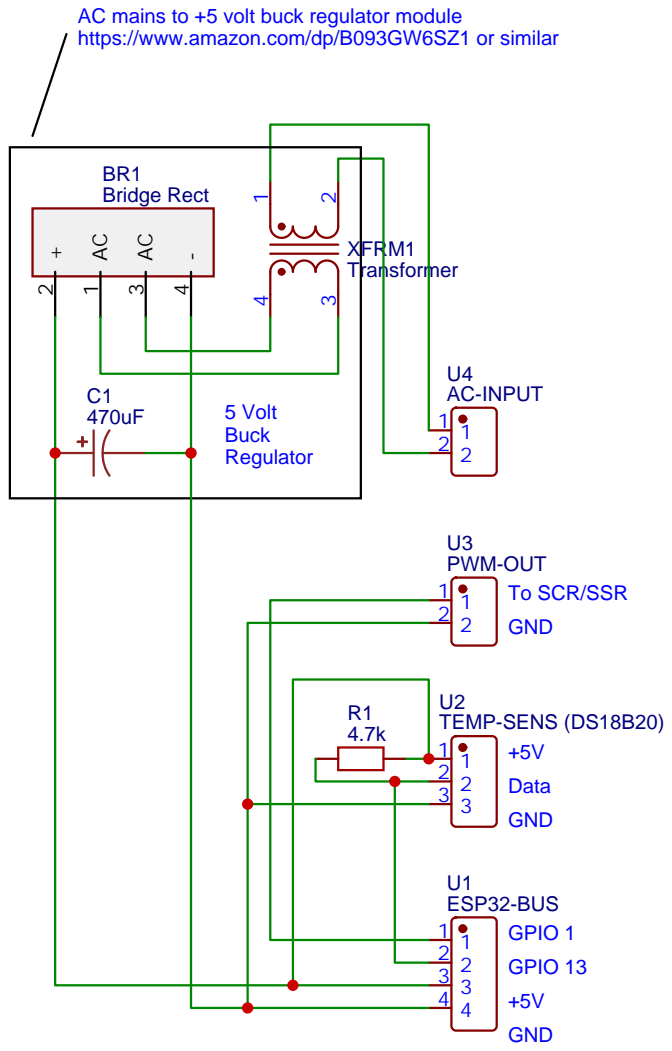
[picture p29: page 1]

AC mains to +5 volt buck regulator module
https://www.amazon.com/dp/B093GW6SZ1 or similar

Drawn By: Larry Athey

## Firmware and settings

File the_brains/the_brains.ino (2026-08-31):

//------------------------------------------------------------------------------------------------
// Airhead - Air Still Brain | (CopyLeft) 2024-Present | Larry Athey (https://panhandleponics.com)
//
// Tested up to Espressif ESP32 v2.0.14 due to LilyGo requirements
//
// This code requires the LilyGo T-Display-S3 ESP32 board. You will first need to properly set up
// your Arduino IDE to upload to that board. See: https://github.com/Xinyuan-LilyGO/T-Display-S3
// Make sure that you only install the Espressif ESP32 v2.0.14 board library since the 3.x stuff
// is not backward compatible and will throw syntax errors all over the place. (Nice fkin upgrade)
//
// This code is written for a 320x170 touch-screen. If you're wanting to use a different ESP32 and
// a larger screen, you'll need to modify a lot of coordinate values in order to use more than the
// upper left corner of a larger screen. Honestly, for as little information that's on the screen,
// I don't see any point in using a larger screen or making it mobile web browser capable.
//
// No, I do not use anybody else's user interface library for the user interface here. They're all
// entirely too bloated for what I need to do. Since I wrote my own GUI for DOS BBS software back
// in the 1990s (MAX Graphics) it wasn't really all that complicated for me to do it again on this
// little computer. It's not flashy, but it's also not unnecessarily bogged down with junk code.
//
// My suggestion for the installation of the temperature sensor is to use one in a TO-92 case and
// attach it to the bolt near the front of the boiler vessel using a transistor chassis mount or
// a copper wiring lug crimped down tight against the temperature sensor. Use wire with silicone
// insulation for all connections and heat shrink the leads to prevent any shorts. You absolutely
// need good thermal transfer compound at all contact points, even around the sensor itself!
//
// This controller will work with any SCR board that accepts a PWM input. If your SCR board uses
// variable voltage, you would just feed a PWM to voltage convertor module between this and your
// your SCR board. Or, if you comment out the SCR_OUT constant definition, you can use this with
// any zero-crossing trigger solid state relay. Absolutely do not use a random-turn-on SSR! SCR
// board or a solid state relay "Boilermaker style", the choice is totally up to you.
//
// You will see that this code has two app modes, Airhead and μBoilermaker. This is toggled from
// one mode to the other by selecting the Mode button on the screen and holding the Value+ button
// for 15 seconds. μBoilermaker uses PID temperature management rather than the PI method used by
// the Airhead mode. This mode is intended for use in a special adaptation of this project built
// into 1500 watt cast iron electric hot plates, commonly used with stove-top stills & brew pots.
//
// NOTE: You can still use a solid state relay in the place of an SCR board, but at a much
//       lower frequency. If your mains power is 50 Hz, then you would use 100 Hz for your
//       PWM frequency. If your mains power is 60 Hz, you would use 120 Hz instead. Please
//       keep in mind that this will cause the SSR to generate more heat, use a heat sink!
//------------------------------------------------------------------------------------------------
#include "Arduino_GFX_Library.h" // Standard GFX library for Arduino, built with version 1.5.9
#include "FreeSans9pt7b.h"       // https://github.com/moononournation/ArduinoFreeFontFile.git 
#include "OneWire.h"             // OneWire Network communications library
#include "DallasTemperature.h"   // Dallas Semiconductor DS18B20 temperature sensor library
#include "Preferences.h"         // ESP32 Flash memory read/write library
#include "Wire.h"                // I2C communications library for touch-screen interface
#define TOUCH_MODULES_CST_SELF   // Tell TouchLib.h to use the CST816 chip routines
#include "TouchLib.h"            // LilyGo touch-screen interface library
#include "QuickPID.h"            // PID calculation library from https://github.com/Dlloydev/QuickPID (used in μBoilermaker mode)
#include "sTune.h"               // QuickPID autotune library from https://github.com/Dlloydev/sTune (used in μBoilermaker mode)
#include "ota_update.h"          // Over-The-Air firmware updating library
#include "ah_splash.h"           // Airhead mode splash screen
#include "ubm_splash.h"          // μBoilermaker mode splash screen
//------------------------------------------------------------------------------------------------
#define ONE_WIRE 13              // 1-Wire network pin for the DS18B20 temperature sensor
//#define SCR_OUT 1              // PWM output to an SCR board (comment out if using a Boilermaker style SSR)
#define FAN_OUT 2                // Cooling fan on/off toggle (optional)
#define SCL 17                   // I2C clock pin
#define SDA 18                   // I2C data pin
#define SCREEN_BACKLIGHT 38      // Screen backlight LED pin
#define SCREEN_POWER_ON 15       // Screen power on/off pin
#define INC_BTN 0                // Value + button
#define DEC_BTN 14               // Value - button
#define TOUCH_INT 16             // CPU interrupt monitor pin for touch-screen input hook
#define TOUCH_RES 21             // Reset pin for touch-screen controller chip
//------------------------------------------------------------------------------------------------
bool ActiveRun = false;          // True if there's an active distillation run
bool ConfigMode = false;         // True if the configuration mode is active
bool GotInterrupt = false;       // True if touch input has been detected on the screen
bool UpToTemp = false;           // True if the run startup has reached operating temperature
bool UpdateMode = false;         // True if the Airhead is running in firmware update mode
unsigned long StartTime = 0;     // Start time of the current distillation run
unsigned long FallBackTime = 0;  // Time of the still finally reached minimum operating temperature
unsigned long LoopCounter = 0;   // Timekeeper for the loop to eliminate the need to delay it
unsigned long LastAdjustment = 0;// Time of the last power adjustment
long Mode3Counter = 0;           // 15 minute timer for mode 3 target temperature adjustments
float TempC = 0;                 // Current temperature reading C
float TempF = 0;                 // Current temperature reading F
float Mode3Temp = 0;             // Current target temperature when running in mode 3
float Mode3Factor = 0;           // How much to increase/decrease the mode 3 target temperature
float Correction = 0.0;          // How much to correct temp sensor C readings (positive or negative)
byte UserTemp1 = 0;              // User selected mode 2 temperature or mode 3 start temperature
byte UserTemp2 = 0;              // User selected ending temperature in mode 3
byte UserTime = 0;               // User selected distillation run time in mode 3 (hours)
byte UserPower = 0;              // User selected power level in mode 1 (0% to 100%)
byte UserMode = 1;               // Last used operation mode selected by the user
byte CurrentMode = 1;            // 1 = Constant Power, 2 = Constant Temp, 3 = Timed w/Temps
byte Mode3Direction = 1;         // Mode 3 temperature direction, 0 = decrease, 1 = increase
byte PowerLevel = 0;             // Current power level 0-255, (100/255) * PowerLevel = % Power
byte StartupPower = 0;           // Startup power percentage in temperature managed modes
byte FallbackPower = 0;          // Fallback power percentage in temperature managed modes
byte RestPeriod = 0;             // How many seconds to rest after the target temperature is reached
byte ActiveButton = 0;           // Currently selected touch-screen button
byte AppMode = 0;                // 0 = Airhead mode, 1 = μBoilermaker mode
char Runtime[10];                // HH:MM:SS formatted time of the current distillation run
String Version = "1.0.2c";       // Current release version of the project
//------------------------------------------------------------------------------------------------
// Coordinates for touch-screen buttons (Modes 1 and 2)
int ModeX1 = 0, ModeY1 = 0, ModeX2 = 158, ModeY2 = 84;
int RunX1 = 160, RunY1 = 0, RunX2 = 319, RunY2 = 84;
int PowerX1 = 0, PowerY1 = 86, PowerX2 = 158, PowerY2 = 169;
int TempX1 = 160, TempY1 = 86, TempX2 = 319, TempY2 = 169;
// Coordinates for Mode 3 bottom row buttons
int StartX1 = 0, StartY1 = 86, StartX2 = 105, StartY2 = 169;
int EndX1 = 107, EndY1 = 86, EndX2 = 213, EndY2 = 169;
int TimeX1 = 215, TimeY1 = 86, TimeX2 = 319, TimeY2 = 169;
// RGB values for the button and text colors
#define MODEBTN RGB565(200,0,200)
#define RUNBTN RGB565(0,215,0)
#define STOPBTN RGB565(230,0,0)
#define PWRBTN RGB565(0,210,210)
#define TEMPBTN RGB565(50,50,230)
#define STARTBTN RGB565(0,210,210)
#define ENDBTN RGB565(0,210,210)
#define TIMEBTN RGB565(50,50,230)
#define HILITE RGB565(230,230,230)
#define BTNTEXT RGB565(245,245,245)
//------------------------------------------------------------------------------------------------
Arduino_DataBus *bus = new Arduino_ESP32PAR8Q(7 /* DC */, 6 /* CS */, 8 /* WR */, 9 /* RD */,39 /* D0 */, 40 /* D1 */, 41 /* D2 */, 42 /* D3 */, 45 /* D4 */, 46 /* D5 */, 47 /* D6 */, 48 /* D7 */);
Arduino_GFX *gfx = new Arduino_ST7789(bus, 5 /* RST */, 0 /* rotation */, true /* IPS */, 170 /* width */, 320 /* height */, 35 /* col offset 1 */, 0 /* row offset 1 */, 35 /* col offset 2 */, 0 /* row offset 2 */);
Arduino_Canvas_Indexed *canvas = new Arduino_Canvas_Indexed(320 /* width */, 170 /* height */, gfx);
TouchLib Touch(Wire,SDA,SCL,CTS820_SLAVE_ADDRESS,TOUCH_RES);
//------------------------------------------------------------------------------------------------
OneWire oneWire(ONE_WIRE);
DallasTemperature DT(&oneWire);
Preferences preferences;
//------------------------------------------------------------------------------------------------
// v1.0.2b add-on to provide PID control in μBoilermaker app mode
float targetTemp = 32.0;         // PID target temperature
float pidOutput = 0.0;           // PID Computed PWM percentage (0-100) 
float Kp = 0.1;                  // PID Proportional gain (0.1 to 10.0)
float Ki = 0.029;                // PID Integral gain (0.001 to 0.5)
float Kd = 0.1;                  // PID Derivative gain (0.0 to 2.0)
float sampleTime = 10.0;         // PID Sample time (5 to 30 seconds)
QuickPID myPID(&TempC,&pidOutput,&targetTemp,Kp,Ki,Kd,
               QuickPID::pMode::pOnMeas,
               QuickPID::dMode::dOnMeas,
               QuickPID::iAwMode::iAwCondition,
               QuickPID::Action::direct);
sTune tuner(&TempC,&pidOutput,
            sTune::ZN_PID,
            sTune::directIP,
            sTune::printSUMMARY);
//------------------------------------------------------------------------------------------------
#ifndef SCR_OUT
#include "esp_timer.h"   // High resolution timer library for use with interrupt driven code
#include "driver/gpio.h" // ESP-IDF GPIO library
//------------------------------------------------------------------------------------------------
#define SSR_OUT GPIO_NUM_1 // Same pin as used with an SCR board

int dutyCyclePercentage = 0;
hw_timer_t *timer = NULL;
//------------------------------------------------------------------------------------------------
void IRAM_ATTR onTimer() { // Custom low frequency PWM designed specifically for SSR usage
  static uint32_t cycleCounter = 0;
  cycleCounter ++;
    
  if (cycleCounter == 10) { // Reset counter every 10 interrupts (equivalent to 2.5 seconds if interrupt every 250ms)
    cycleCounter = 0;
  }

  if (cycleCounter < (dutyCyclePercentage / 10.0)) { // Turn on if within duty cycle
    gpio_set_level(SSR_OUT,1);
  } else {
    gpio_set_level(SSR_OUT,0);
  }
}
#endif
//------------------------------------------------------------------------------------------------
void setup() {
  // Enable serial communications for debugging output
  Serial.begin(9600);
  delay(1000);
  Serial.println("");

  // Get the last user settings from flash memory
  GetMemory();
  if (UserTemp1 == 0) {
    // System reset initiated or this is a new chip, initialize the flash memory
    UserTemp1     = 80;
    UserTemp2     = 86;
    UserTime      = 2;
    UserPower     = 80;
    UserMode      = 1;
    Correction    = 0.0;
    StartupPower  = 50;
    FallbackPower = 33;
    RestPeriod    = 60;
    Kp            = 2.0;
    Ki            = 0.005;
    Kd            = 1.0;
    SetMemory();
  }
  CurrentMode = UserMode;

  // Initialize the touch-screen reset line
  pinMode(TOUCH_RES,OUTPUT);
  digitalWrite(TOUCH_RES,LOW);
  delay(500);
  digitalWrite(TOUCH_RES,HIGH);

  // Initialize the optional fan toggle pin
  pinMode(FAN_OUT,OUTPUT);
  digitalWrite(FAN_OUT,LOW);

  // Initialize all of the necessary GPIO libraries
  DT.begin();
  Wire.begin(SDA,SCL);
  if (Touch.init()) {
    Serial.println("Touch screen interface initialized");
    attachInterrupt(TOUCH_INT,[] { GotInterrupt = true; },FALLING);
  } else {
    Serial.println("Touch screen interface not detected");
  }

  // Power up the screen and backlight
  pinMode(SCREEN_POWER_ON,OUTPUT);
  digitalWrite(SCREEN_POWER_ON,HIGH);
  ledcSetup(0,2000,8);
  ledcAttachPin(SCREEN_BACKLIGHT,0);
  ledcWrite(0,255); // Screen brightness (0-255)

  // Initialize the graphics library and blank the screen
  gfx->begin();
  gfx->setRotation(3);
  gfx->fillScreen(BLACK);

  // In order to eliminate screen flicker, everything is plotted to an off-screen buffer and popped onto the screen when done
  canvas->begin();
  canvas->fillScreen(0); 
  const uint16_t* bitmap = nullptr;
  if (AppMode == 0) {
    bitmap = Airhead;
  } else {
    bitmap = uBoilermaker;
    myPID.SetOutputLimits(0,100);
    myPID.SetSampleTimeUs(sampleTime * 1000000);
  }
  gfx->draw16bitRGBBitmap(0,0,(uint16_t*)bitmap,320,170);
  gfx->setFont(&FreeSans9pt7b);
  gfx->setTextColor(WHITE);
  gfx->setCursor(245,158);
  gfx->print("v" + Version);
  delay(5000);
  canvas->flush();
  ScreenUpdate();

  #ifndef SCR_OUT
  gpio_set_direction(SSR_OUT,GPIO_MODE_OUTPUT);
  gpio_set_level(SSR_OUT,0);
  // Air Still heating elements have a slow reaction time, an SCR's switching frequency is wasteful
  // Therefore, a custom low frequency PWM driving a solid state relay is a better option
  timer = timerBegin(0,80,true); // Timer at 1 MHz, count up
  timerAttachInterrupt(timer,&onTimer,true); // Attach the PWM toggle function
  timerAlarmWrite(timer,250000,true); // Timer trigger set to 250ms (250,000 microseconds)
  timerAlarmEnable(timer); // Now enable the low frequency pulse width modulator
  #else
  // Assign the SCR controller output pin to a PWM channel
  // For heating elements, 1 KHz to 3 KHz is used, adjust as necessary
  ledcSetup(1,2000,8);
  ledcAttachPin(SCR_OUT,1);
  ledcWrite(1,0);
  #endif

  // Initialize the timing related variables
  LoopCounter = millis();
  LastAdjustment = LoopCounter;

  // If the Value- is being pressed, activate the firmware update mode
  if (digitalRead(DEC_BTN) == 0) {
    UpdateMode = true;
    PopoverMessage("Firmware Update Mode");
    Serial.println("Starting Airhead Firmware Updater (AP mode)...");

    // Start WiFi Access Point
    WiFi.mode(WIFI_AP);
    WiFi.softAP(ap_ssid,ap_password);
    IPAddress myIP = WiFi.softAPIP();
    Serial.print("AP IP address: ");
    Serial.println(myIP);

    // Start Bonjour/ZeroConf
    if (MDNS.begin("esp32")) {
      Serial.println("mDNS started - http://esp32.local");
    }

    // Set the server home page, sent upon browser connection
    server.on("/",HTTP_GET,[]() {
      server.send(200,"text/html",serverIndex);
    });

    // Set the OTA firmware update handler
    server.on("/update",HTTP_POST,[]() {
      server.sendHeader("Connection","close");
      server.send(200,"text/plain",(Update.hasError()) ? "FAIL" : "OK");
      ESP.restart();
    },[]() {
      HTTPUpload& upload = server.upload();
      if (upload.status == UPLOAD_FILE_START) {
        Serial.printf("Update: %s\n",upload.filename.c_str());
        if (!Update.begin(UPDATE_SIZE_UNKNOWN)) {
          Update.printError(Serial);
        }
      } else if (upload.status == UPLOAD_FILE_WRITE) {
        if (Update.write(upload.buf,upload.currentSize) != upload.currentSize) {
          Update.printError(Serial);
        }
      } else if (upload.status == UPLOAD_FILE_END) {
        if (Update.end(true)) {
          Serial.printf("Update Success: %u bytes\n",upload.totalSize);
        } else {
          Update.printError(Serial);
        }
      }
    });

    server.begin();
    Serial.println("HTTP server ready. Connect to the AP and go to 192.168.4.1");
  }
}
//------------------------------------------------------------------------------------------------
void GetMemory() { // Get the last user settings from flash memory on startup
  preferences.begin("prefs",true);
  UserTemp1     = preferences.getUInt("usertemp1",0);
  UserTemp2     = preferences.getUInt("usertemp2",0);
  UserTime      = preferences.getUInt("usertime",0);
  UserPower     = preferences.getUInt("userpower",0);
  UserMode      = preferences.getUInt("usermode",0);
  Correction    = preferences.getFloat("correction",0.0);
  StartupPower  = preferences.getUInt("startuppower",50);
  FallbackPower = preferences.getUInt("fallbackpower",33);
  RestPeriod    = preferences.getUInt("restperiod",60);
  AppMode       = preferences.getUInt("appmode",0);
  Kp            = preferences.getFloat("pid_kp",2.0);
  Ki            = preferences.getFloat("pid_ki",0.005);
  Kd            = preferences.getFloat("pid_kd",1.0);
  preferences.end();
}
//------------------------------------------------------------------------------------------------
void SetMemory() { // Update flash memory with the current user settings
  preferences.begin("prefs",false);
  preferences.putUInt("usertemp1",UserTemp1);
  preferences.putUInt("usertemp2",UserTemp2);
  preferences.putUInt("usertime",UserTime);
  preferences.putUInt("userpower",UserPower);
  preferences.putUInt("usermode",UserMode);
  preferences.putFloat("correction",Correction);
  preferences.putUInt("startuppower",StartupPower);
  preferences.putUInt("fallbackpower",FallbackPower);
  preferences.putUInt("restperiod",RestPeriod);
  preferences.putUInt("appmode",AppMode);
  preferences.putFloat("pid_kp",Kp);
  preferences.putFloat("pid_ki",Ki);
  preferences.putFloat("pid_kd",Kd);
  preferences.end();
}
//------------------------------------------------------------------------------------------------
void TempUpdate() { // Update the temperature sensor values
  DT.requestTemperatures();
  float Test = DT.getTempCByIndex(0); // Returns -127.00 if the device reading fails
  if (Test > -127.00) {
    TempC = Test;
    TempC += Correction;
  }
  TempF = TempC * 9 / 5 + 32;
  Serial.print("Temp C: "); Serial.println(TempC);
  Serial.print("Temp F: "); Serial.println(TempF);
}
//-----------------------------------------------------------------------------------------------
void PowerAdjust(byte Percent) { // Set the SCR board or SSR timing to a target power percentage
  Serial.print("Power Adjust: "); Serial.println(Percent);
  LastAdjustment = millis();
  #ifndef SCR_OUT
  // This is a digital power controller, there are only on and off states
  dutyCyclePercentage = Percent;
  PowerLevel = round(Percent * 2.55);
  #else
  // This is an analog power controller, first set the power level to zero
  // and rest 1 second so all of the capacitors can fully discharge
  ledcWrite(1,0);
  delay(1000);
  // Then progressively adjust the power level up to the requested percentage
  if (Percent > 0) {
    PowerLevel = round(Percent * 2.55);
    float x = 2.55;
    while (x <= PowerLevel) {
      ledcWrite(1,x); // Function appears to round x on its own, no errors thrown
      delay(10);
      x += 2.55;
    }
  } else {
    PowerLevel = 0;
  }
  #endif
}
//-----------------------------------------------------------------------------------------------
void RunState(byte State) { // Toggle the active distillation run state
  if (State == 1) {
    StartTime = millis();
    ActiveRun = true;
    UpToTemp  = false;
    digitalWrite(FAN_OUT,HIGH);
    if (CurrentMode > 1) {
      if (CurrentMode == 3) {
        byte Range;
        if (UserTemp1 < UserTemp2) {
          Mode3Direction = 1;
          Mode3Temp = float(UserTemp1);
          Range = UserTemp2 - UserTemp1;
        } else {
          Mode3Direction = 0;
          Mode3Temp = float(UserTemp2);
          Range = UserTemp1 - UserTemp2;
        }
        Mode3Factor  = float(Range) / float(UserTime * 4);
        Mode3Counter = millis();
      }
      if (AppMode == 1) {
        if (CurrentMode == 3) {
          targetTemp = Mode3Temp;
        } else {
          targetTemp = float(UserTemp1);
        }
        myPID.Reset();
        myPID.SetTunings(Kp,Ki,Kd);
        myPID.SetMode(myPID.Control::manual);
        PowerAdjust(10);
      } else {
        PowerAdjust(StartupPower);
      }
    } else {
      PowerAdjust(UserPower);
    }
  } else {
    ActiveRun = false;
    PowerAdjust(0);
    digitalWrite(FAN_OUT,LOW);
  }
}
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
void loop() {

}
*/
//------------------------------------------------------------------------------------------------

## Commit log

2024-11-29 Create Full Spacer Ring.stl
    [Full Spacer Ring.stl]
2024-11-29 Create Spacer Ring Half - 1.stl
    [Spacer Ring Half - 1.stl]
2024-11-29 Create Spacer Ring Half - 2.stl
    [Spacer Ring Half - 2.stl]
2024-11-29 Create Airhead Button.stl
    [Airhead Button.stl]
2024-11-29 Create Airhead Case Back.stl
    [Airhead Case Back.stl]
2024-11-29 Create Airhead Case Front.stl
    [Airhead Case Front.stl]
2024-12-13 Create Spacer Ring Full.stl
    [Spacer Ring Full.stl]
2024-12-13 Create Spacer Ring Half.stl
    [Spacer Ring Half.stl]
2026-04-11 Create Airhead Inside Plate.stl
    [Airhead Inside Plate.stl]
2026-05-01 Added hidden μBoilermaker mode
2026-05-01 Hidden μBoilermaker mode update
2026-05-04 Add μBoilermaker case 3D models
    [uBM-Corner-Cap.stl, uBM-Fan-Cover.stl]
2026-05-14 PID autotune update
